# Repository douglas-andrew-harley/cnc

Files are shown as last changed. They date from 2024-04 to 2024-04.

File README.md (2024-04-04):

# FCCH CNC files

This repo contains archives of information related to the various CNC machines
at the Creator Hub. Each machine's data is in a separate top-level directory.
Within each directory, there are various sub-directories for hardware design,
software config files, etc.

## Wood-48x48

CNC Router in wood shop.

## Metal_mill

Donated 3-axis mill previously retrofitted for CNC.  The controller was old and did not work with LinuxCNC and it also was just mounted on a plate and not enclosed so we built a new controller modelled after the Wood-48x48 controller.  This folder contains the design and documentation for that new controller cabinet.

[metal_mill README](metal_mill/README.md)

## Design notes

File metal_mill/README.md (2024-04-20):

# Metal Mill CNC Controller

This project is a CNC controller for a mill or other 3 axis machaine that uses 35V-40V DC servo motors.

It consists of 2 parts

1) a controller cabinet that controls the motors in accordance to instructions from a computer running LinuxCNC and
2) an RFID and E-Stop module that connects to the controller cabinet to controll whether the servo drives are enabled.

Design File PDFs

* [metal_mill_wiring.sch (pdf)](metal_mill_wiring.pdf) (created in EagleCAD)
* [FCCH_RFID_ESTOP.sch (pdf)](FCCH_RFID_ESTOP.sch.pdf) (created in EagleCAD)
* [FCCH_RFID_ESTOP.brd (pdf)](FCCH_RFID_ESTOP.brd.pdf) (created in EagleCAD)
* [FCCH_RFID_ESTOP.brd (fab print pdf)](FCCH_RFID_ESTOP.brd.fab.pdf) (created in EagleCAD)
* [panel_cutouts.FCStd (pdf)](panel_cutouts.pdf) (created in FreeCAD)

## Controller Cabinet Components

* (1) 7i96s Controller
* (3) G320X - Gecko DC Servo Drive
* (1) NSP-1600-36 Power Supply
* (1) 12V to 5V buck Converter
* (4) Panel mount GX16-8 Aviation Connectors
* (6) Panel mount 3.5mm mono jacks with plug detection (3 terminal)
* (1) Panel mount A/C C-14 reciptical
* (3) Power Bus Bars (at least 5 position)
* (1) case (we are using a salvaged desktop PC)
* (1) panel for connectors

### 7i96s Controller

This is a card that provides IO and axis drive output for LinuxCNC.  The card connects to a PC via a point to point (no switch) dedicated Ethernet.  This project describes how the inputs and outputs of the 7i96s should be connected to interface with the mill.

Input Summary

* INPUT0: Drive Power OK<br>
  High (3.5 ~ 5.5V) : When the Vout ≦ 77% ± 5%.<br>
  Low (-0.5 ~ 0.5V) : When Vout ≧ 80% ± 5%.
* INPUT1: Drive Power T-Alarm<br>
  High (3.5 ~ 5.5V) : When the internal temperature exceeds the limit of temperature alarm, or when Fan fails.<br>
  Low (-0.5 ~ 0.5V) : When the internal temperature is normal, and when Fan normally works.
* INPUT2: Xmin limit switch (normally open)
* INPUT3: Xmax limit switch (normally open)
* INPUT4: Ymin limit switch (normally open)
* INPUT5: Ymax limit switch (normally open)
* INPUT6: Zmin limit switch (normally open)
* INPUT7: Zmax limit switch (normally open)
* INPUT8: X drive OK/Fault High==OK
* INPUT9: Y drive OK/Fault High==OK
* INPUT10: Z drive OK/Fault High==OK
* IN_COM: +5V (all inputs will be 0-5V)

Output Summary

* OUT0: Reset Drivers. Hold high for at least 1 sec to reset X,Y, and Z drivers to clear a fault on any or all drivers. INPUTs 8,9,10 read the OK/fault state of the X,Y,Z drivers respectively.
* OUT1: Motor Power Enable.
* Stepper Drive Units 0-2 connect to the 3 G320X drivers

### G320X - Gecko DC Servo Drive

The 7i96s provides stepper motor outputs for the drives but the mill we are using has DC servo motors installed.  The G320X provides translation between the stepper motor signals and DC servo motor control. Each servo motor connects to a G320X via 2 dc power wires and 4 encoder wires. The encoder provides feedback to the G320X so that it can determine what power to send to the motor to make its position match the position specified by LinuxCNC.

The G320X drives the motors with a PID controll. There are three screw pots to adjust the position, integral, and derivated gains. When the mill is operational, each axis needs to be tuned to minimize the error.

<https://www.youtube.com/watch?v=Ic4CvIOm6O4>

### NSP-1600-36 Power Supply

This PS provides up to 500W to each of the X,Y,Z drives at an adjustable voltage between 35V and 40V. The mill's X axis motor is rated at 38V and the Y axis is rated at 40V so we can adjust the voltage to 39V to split the difference. The Z axis motor is not easily accessible so we assume its either 38 or 40V. 

The main power can be turned on and off independent of the allways on aux power (12V@850ma) which we use to power all the components in the cabinet and the E-Stop RFID module.

The PS has a 16 pin connector that provides the aux power and control signals which we interface through the 7i96s so that Linux CNC can controll if the drive power is on or off and determine its status.

### 12V to 5V buck Converter

The aux power from the NSP-1600-36 is 12V but the 7i96s requires 5V.

### Panel mount GX16-8 Aviation Connectors

Each axis motor is connected to the controller cabinet via a GX16-8 Aviation connector. These connectors are panel mount and screw on for a secure connection. They are avaiable with even number of connectors. We need 7 so we got the 8 conductor. 

We terminate two separate cables into the GX16-8

1) 14 gauge 2 conductor cable for motor power A 38V@500W motor can draw up to 12.5A which requires 14 gauge wires for the 2 motor power wires. 
2) 22 gauge 5 conductor cable for the motor encoder signals and a separate motor housing ground wire. The encoder on these motors use single ended singles so require 4 wires. Since the encoders are single ended (not differential), the encoder cables should be shielded with the shield connected to the case ground on the cabinet side and left unconnected on the motor side. The encoder cable should also have a 5th conductor which is connected to the power supply ground in the cobinet and to the motor housing.

### Panel mount 3.5mm mono jacks with plug in detection

The limit switches are connected to the controller cabinet via 3.5mm mono plugs/jacks. 3 terminal jacks are used where the third terminal makes contact with the tip terminal when no jack is inserted. This is used so that when the jack is removed, it will complete the circuit as if the limit switch was activated. This makes it so that if a limit switch is removed, LinuxCNC will think that the limit switch is tripped and will not drive the machine in that direction. 

### Panel mount A/C C-14 reciptical

This is a stanard reciptical for connecting a device to building power.

### Power Bus Bars

To be sourced...

To connect components to GND, +5V and +12V, we use 3 bus bars that can terminate bare wire leads.

### Case

We are using an old desktop PC from a thrift store.  An alarm panel case or similar would also be suitable.

### Panel for connectors

The file [panel_cutouts.FCStd](panel_cutouts.pdf) (created with FreeCAD) documents the panel cutouts to accept the various panel mount jacks the cabinet uses to connect to the motors, limit switches, FCCH_RFID_ESTOP_module, power, and Ethernet to the computer running LinuxCNC

## Controller Cabinet Cable Harnesses

Inside the controller cabinet, all components are connected via the following wire harnesses. The Wn label of each harness refers to the designation in the schematic.

The schematic [metal_mill_wiring.sch (pdf)](metal_mill_wiring.pdf) (created in EagleCAD) documents the connections.

### Cables required

* 22 gauge 6 conductor cable
* 22 gauge 4 conductor cable
* 22 gauge 2 conductor cable
* 22 gauge single black wire
* 18 gauge 2 conductor red/black
* 18 gauge 3 conductor red/orange/black
* 14 gauge 2 conductor red/black
* 14 gauge 3 conductor line cord

### (W1) Stepper and reset cables from 7i96s to each of the G320X servo drives

3 needed
bare leads to bare leads

* 22 gauge 4 conductor cable
  * one end: bare leads into the terminals on the G320X's
    * cable shield: no connection (only connect on other end)
    * black:  COM
    * blue:   STEP
    * yellow: DIR
    * orange: ERR/RES
  * other end: bare leads into the 7i96s TB3 and TB3 terminals (see schematic)
    * cable shield: connect to chassis ground screw located near the 7i96s
    * black:  TB1 GND(n)
    * blue:   TB1 STEP(n)+
    * yellow: TB1 DIR(n)+
    * orange: TB3 INPUT8 (ERR/RES input)

Build Notes:

We used a shielded 8 conductor wire because the maker space had a big spool of it. The 4 unused conductors were cut short and sealed under a short piece of heat shrink.

On the 7i96s end, the orange and shield wires need to be about 4 inches longer than the others because they go to different places. Strip 5 inches of the cable insulation. cut black,blue,yellow wires to about 1.25 inches. Heat shrink a 3/8 inch tube so that half is over the insulation and half is over the protrubing wires. 

On the G320X end, the orange wire needs to be longer than the others by about an inch. Strip a little over 2 inches of insulation. Cut the shield wire short to the insulation (wont be connected on this end). Cut the black,blue, and yellow wires to about an inch. Heat shrink about 3/8 inch tube over the insulation and wires.

### (W2) Motor Power and Encoder Jacks

3 needed
GX16-8 Aviation connector to 3 separate cables with bare leads

* 14 gauge 2 conductor red/black
  * one end: solder to GX16-8
    * black: terminal 1
    * red:   terminal 2
  * other end: bare leads screw into G320X terminals
    * black: arm-
    * red:   arm+
* 22 gauge 4 conductor cable
  * one end: solder to GX16-8
    * C1: terminal 4
    * C2: terminal 5
    * C3: terminal 6
    * C4: terminal 7
  * other end: bare leads to G320X screw terminals
    * C1: ENC_GND
    * C2: ENC_5VDC
    * C3: Channel_A
    * C4: Channel_B
* 22 gauge single black wire
  * one end: solder to GX16-8
    * terminal 8
  * other end connects to the 9 position gnd bus bar located near the panel

### (W3) E-Stop and RFID Module Jacks

1 needed
GX16-8 Aviation connector to 2 separate cables

* 18 gauge 3 conductor red/orange/black
  * one end: solder to GX16-8
    * black:  terminal 1
    * red:    terminal 2
    * orange: terminal 3
  * other end: bare leads to GND,+5V, and +12V bus bars
* 22 gauge 6 conductor cable
  * one end: solder to GX16-8
    * C1: terminal 4
    * C2: terminal 5
    * C3: terminal 6
    * C4: terminal 7
    * C5: terminal 8
    * C6: N/C

### (W4) Limit Switch Panel Mount Jacks

1 needed
6x 3.5 mono panel mount jacks to 6x ground wires and 1x 6 conductor cables with bare leads

* 6x 22 gauge single black wire connects each jack terminal 1 and 2 and then to the 9 position gnd bus bar located near the panel.
* 1x 22 gauge 6 conductor cable
  * one end: solder to terminal 3 on each jack
  * other end: bare leads connect to 7i96s screw terminals
    * Xmin: TB3.3 (INPUT2)
    * Xmax: TB3.4 (INPUT3)
    * Ymin: TB3.5 (INPUT4)
    * Ymax: TB3.6 (INPUT5)
    * Zmin: TB3.7 (INPUT6)
    * Zmax: TB3.8 (INPUT7)

### (W5) Servo Driver Power

1 needed
2 circular lug crimp connectors to 3x 2 conductor cables with bare leads

* 3x 14 gauge 2 conductor red/black
  * one end collect the 3 red wires together into a circular crimp lug connector. do the same with the balck cables. The two circular connects will be bolted to the main PS lugs
  * other ends of the 3 cables has bare leads to screw into the PWR_GND (black) and 18V_to 80V_PWR terminal of the 3 G320X servo drivers

### (W6) A/C Input to PS

1 needed
crimp spade connectors to crimp spade connectors

* 14 gauge 3 conductor line cord

### (W7) Power Supply signals

1 needed
HRS DF11-16DS 16 pin IDC to bare leads

* 18 gauge 2 conductor red/black
  * one end: IDC pins inserted in 16x connector
    * red  : pin 1
    * black: pin 2
  * other end: bare leads to GND and 12V bus bars
* 22 gauge 4 conductor cable
  * one end: IDC pins inserted in 16x connector
    * C1: pin 3
    * C2: pin 4
    * C3: pin 5
    * C4: pin 6
  * other end: bare leads screwed into 7i96s terminals
    * C1: TB3-16 (OUT1+)
    * C2: TB3-15 (OUT1-)
    * C3: TB3-1  (INPUT0)
    * C4: TB3-2  (INPUT1)

Note that the DF11-16DS connector on the PS has 16 positions. 1-6 are connected as above. In addition, two loop back wires on the connector are needed to connect positions 13 to 15, and 14 to 16. The PS came with a connector that had these loop back wires already installed. These loopback wires implement the local voltage sensing as described in the datasheet. If we ever want to implement remote sensing to compensate for drops seen at the motors, we would replace theses loopbacks with wires connecting 15 and 16 to the + and - motor leads.

### (W8) 7i96s Power

1 needed
bare leads to bare leads

* 18 gauge 2 conductor red/black

## E-Stop and RFID Module (FCCH_RFID_ESTOP)

This is a custom PCB in a separate enclosure that can be mounted in a accessible location on the mill for the operator to interact with. The enclosure contains this custom PCB and also the FCCH RFID PCB. An 8 pin GX16-8 Aviation connector connects this enclosure with the controller cabinet.

The FCCH_RFID_ESTOP module provides two functions.

1) RFID Authorization. Major machines at the FCCH (fort Collins Creator Hub) have RFID based access control. When an authorized RFID tag is not present in the V slot of this module, the axis motors are inhibited.
2) E-Stop switch. If the E-Stop is pressed, the axis motors are inhibited.

The ERR/RES lines of the G320X drivers are brought to this module. They are attached to ground (which inhibits the drivers) through the normally closed contacts of a safety relay. When both a valid RFID tag is present and the E-Stop switch is not active, the relay is energized, breaking the connection to ground and enabling the drivers.

The file [FCCH_RFID_ESTOP.sch (pdf)](FCCH_RFID_ESTOP.sch.pdf) contains the schematic for the custom PCB and [FCCH_RFID_ESTOP.brd (pdf)](FCCH_RFID_ESTOP.brd.pdf) is the board layout.

For physical dimensions of the board refer to [FCCH_RFID_ESTOP.brd.fab.pdf](FCCH_RFID_ESTOP.brd.fab.pdf)

## FCCH_RFID_ESTOP Cable Harnesses

### (EW1) GX16-8 connector to FCCH_RFID_ESTOP board

1 needed
GX16-8 panel mount side to bare leads

* Ethernet cable soldered to the panel mount. Wires connected per schematic to screw terminals of the FCCH_RFID_ESTOP board.

### (EW2) FCCH_RFID_ESTOP board to FCCH_RFID board

1 needed
bare leads to bare leads

* 22 gauge 4 conductor cable

### (EW3) Controller Cabinet to FCCH_RFID_ESTOP module

1 needed
GX16-8 to GX16-8

Ethernet cable soldered to the free hanging side of the GX16-8 connects. All pins pass through straight.

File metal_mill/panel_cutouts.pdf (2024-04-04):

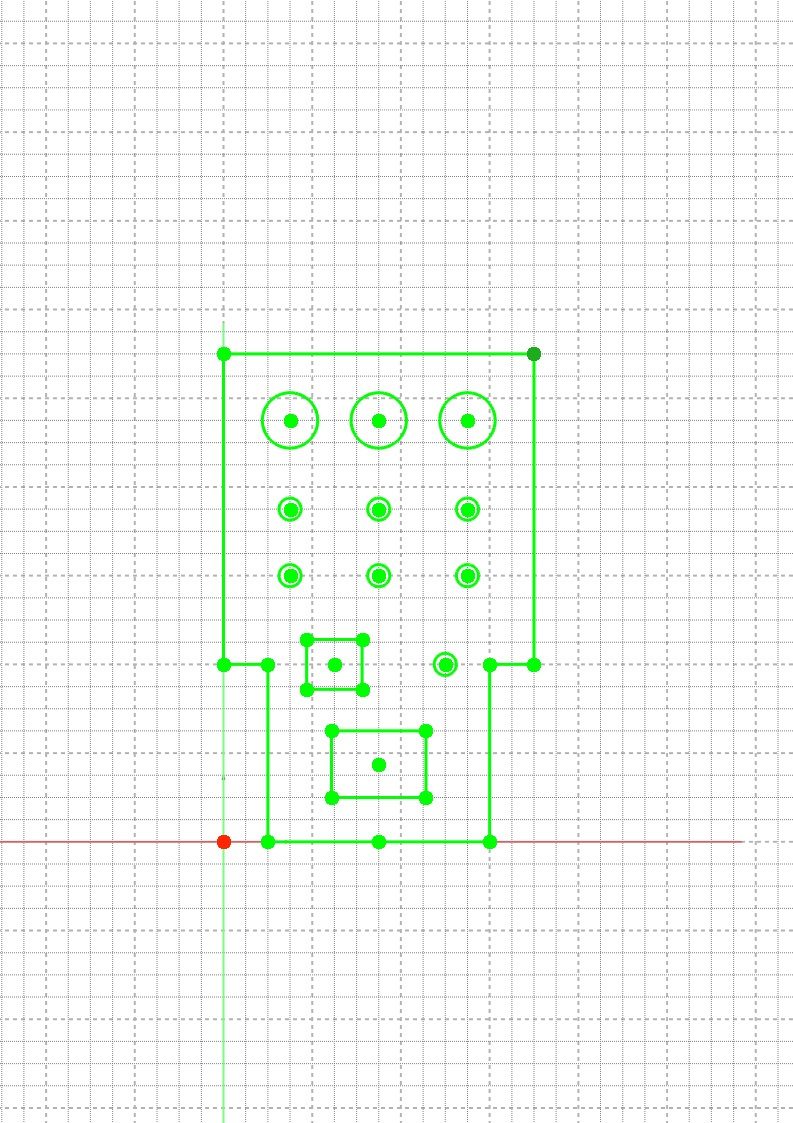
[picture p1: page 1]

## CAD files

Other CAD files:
metal_mill/panel_cutouts.FCStd

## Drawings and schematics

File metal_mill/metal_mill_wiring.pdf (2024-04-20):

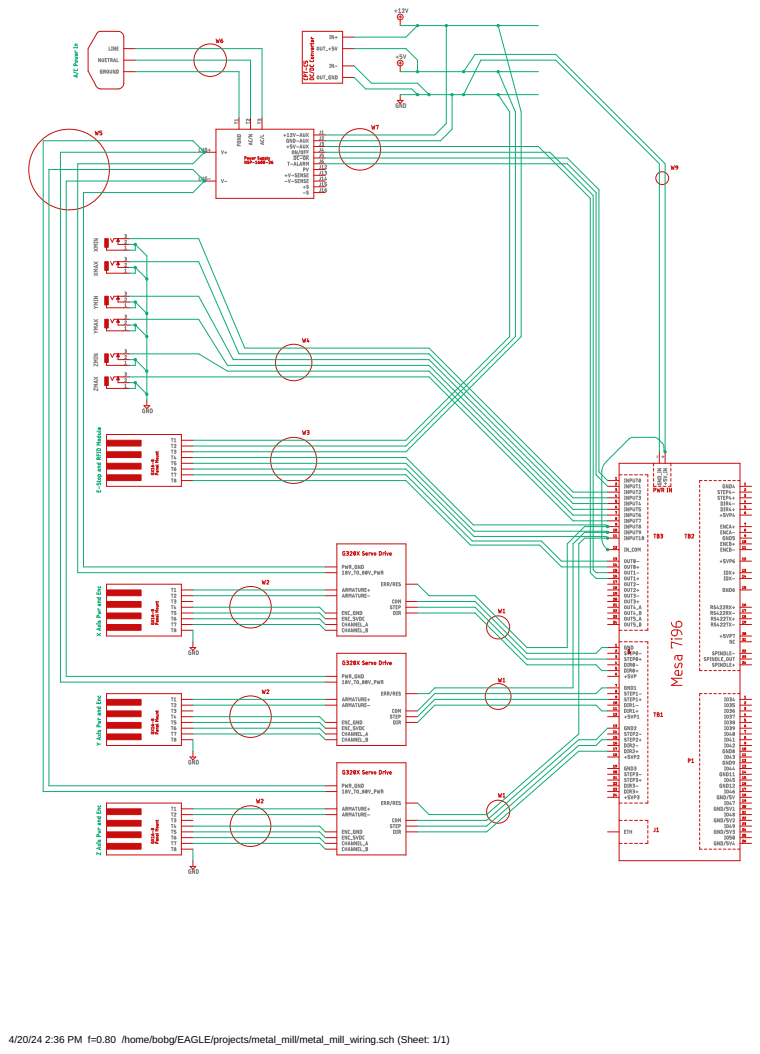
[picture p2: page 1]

4/20/24 2:36 PM f=0.80 /home/bobg/EAGLE/projects/metal_mill/metal_mill_wiring.sch (Sheet: 1/1)

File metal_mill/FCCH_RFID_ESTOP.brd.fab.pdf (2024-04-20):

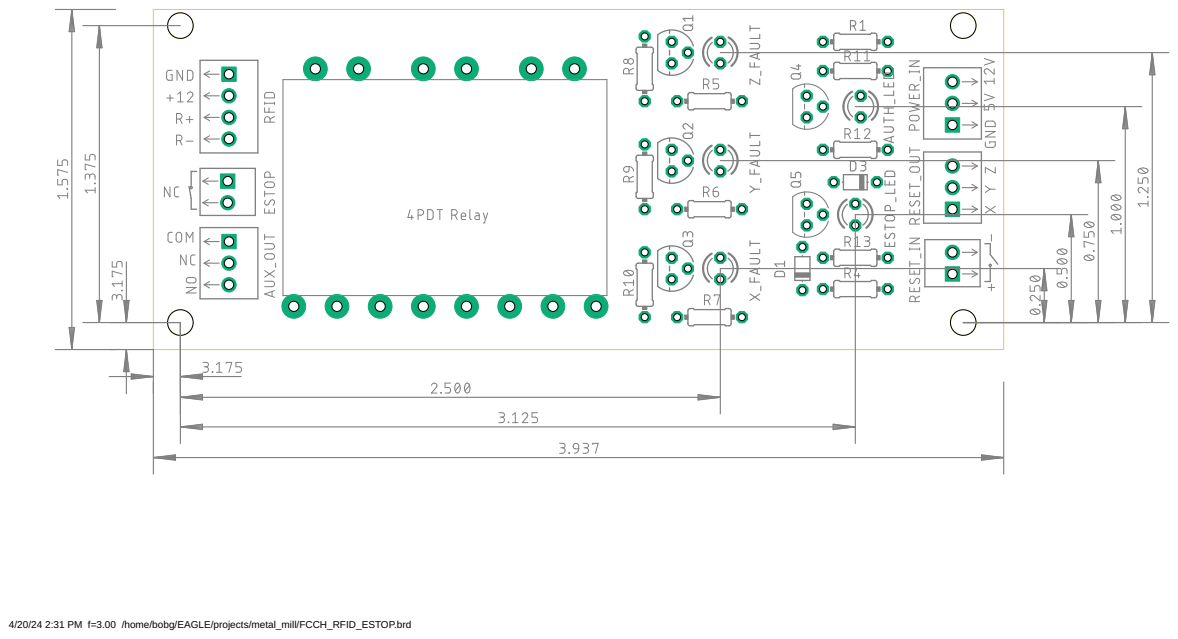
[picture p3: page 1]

4/20/24 2:31 PM f=3.00 /home/bobg/EAGLE/projects/metal_mill/FCCH_RFID_ESTOP.brd

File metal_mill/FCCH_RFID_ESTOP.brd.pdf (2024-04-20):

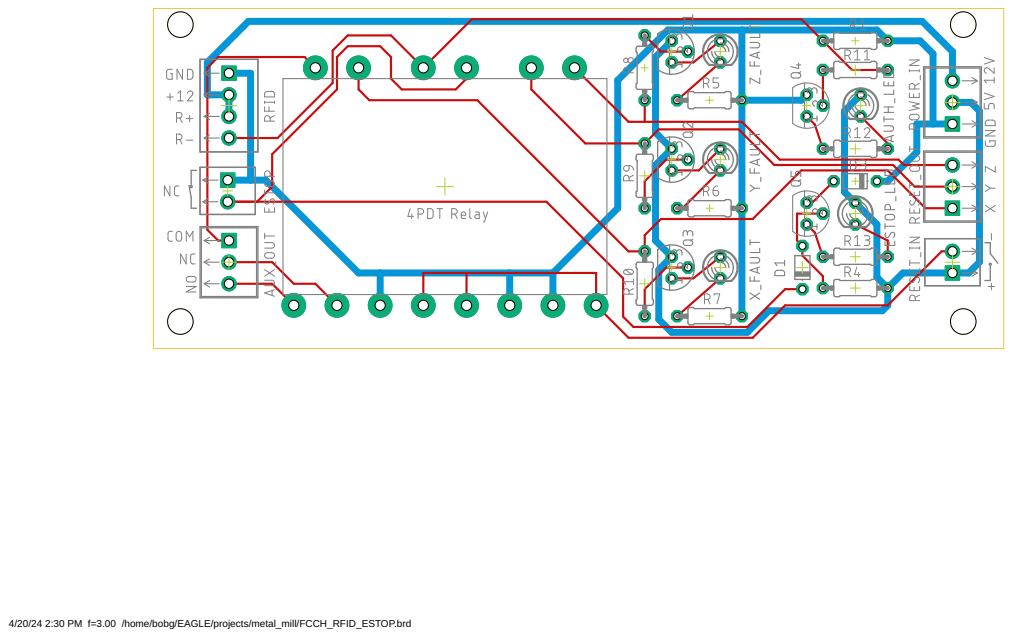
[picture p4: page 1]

4/20/24 2:30 PM f=3.00 /home/bobg/EAGLE/projects/metal_mill/FCCH_RFID_ESTOP.brd

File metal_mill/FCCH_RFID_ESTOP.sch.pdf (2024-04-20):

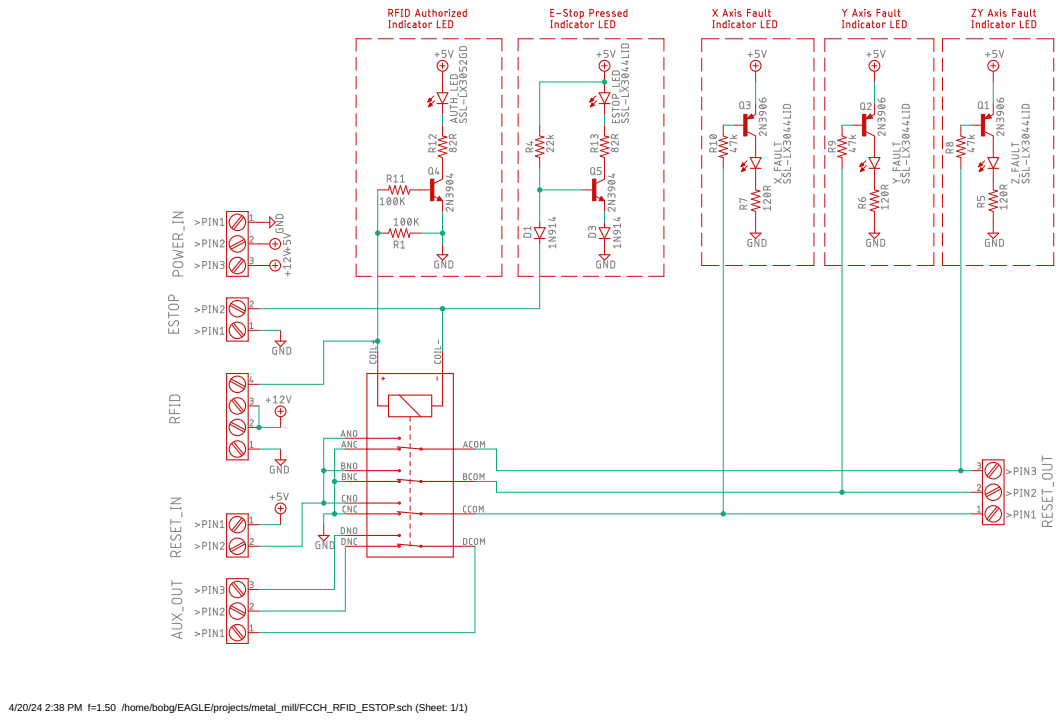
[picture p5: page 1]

4/20/24 2:38 PM f=1.50 /home/bobg/EAGLE/projects/metal_mill/FCCH_RFID_ESTOP.sch (Sheet: 1/1)

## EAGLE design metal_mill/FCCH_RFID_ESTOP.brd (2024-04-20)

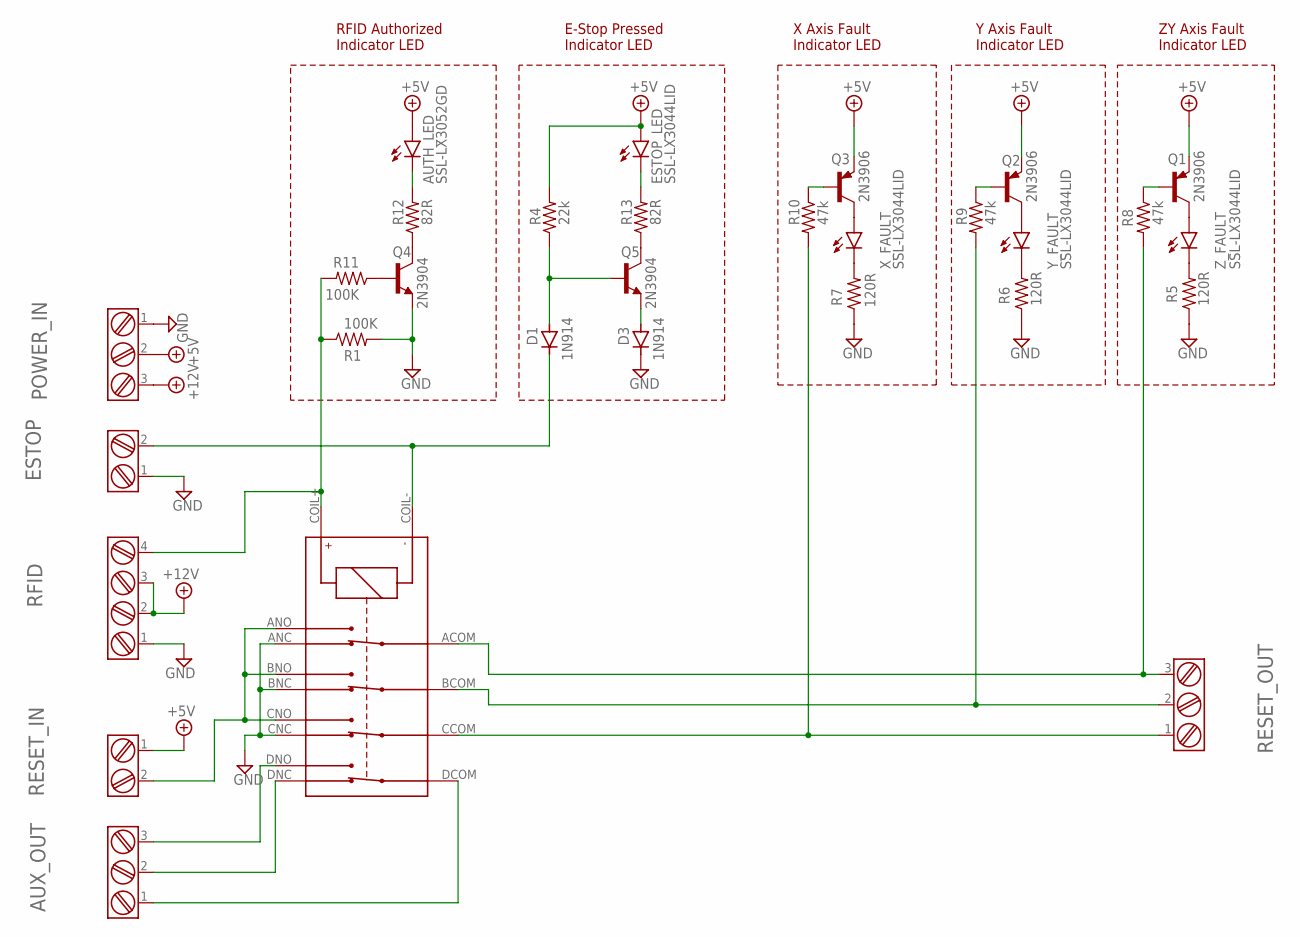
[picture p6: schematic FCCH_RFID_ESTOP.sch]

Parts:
AUTH_LED: SSL-LX3052GD; LED3MM
AUX_OUT: EURO-CON-3_2.54P; CONN3-2.54P
D1, D3: 1N914; D-5
ESTOP: EURO-CON-2_2.54P; CONN2_2.54P
ESTOP_LED: SSL-LX3044LID; LED3MM
POWER_IN: EURO-CON-3_2.54P; CONN3-2.54P
Q1, Q2, Q3: 2N3906; TO92
Q4, Q5: 2N3904; TO92
R1, R11: 100K; 0204/7
R4: 22k; 0204/7
R5, R6, R7: 120R; 0204/7
R8, R9, R10: 47k; 0204/7
R12, R13: 82R; 0204/7
RESET_IN: EURO-CON-2_2.54P; CONN2_2.54P
RESET_OUT: EURO-CON-3_2.54P; CONN3-2.54P
RFID: EURO-CON-4_2.54P; CONN4-2.54P
U$1: NC4D-JP-DC5V; NC4D-JP
X_FAULT: SSL-LX3044LID; LED3MM
Y_FAULT: SSL-LX3044LID; LED3MM
Z_FAULT: SSL-LX3044LID; LED3MM

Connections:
+5V: AUTH_LED.A, ESTOP_LED.A, POWER_IN.2, Q1.3 (E), Q2.3 (E), Q3.3 (E), R4.2, RESET_IN.1
+12V: POWER_IN.3, RFID.2, RFID.3
AUX_RELAY_COM: AUX_OUT.1, U$1.DCOM
AUX_RELAY_NC: AUX_OUT.2, U$1.DNC
AUX_RELAY_NO: AUX_OUT.3, U$1.DNO
ESTOP: D1.C, ESTOP.2, U$1.COIL-
GND: D3.C, ESTOP.1, POWER_IN.1, Q4.3 (E), R1.2, R5.1, R6.1, R7.1, RFID.1, U$1.ANC, U$1.BNC, U$1.CNC
unnamed: R7.2, X_FAULT.K (C)
unnamed: RESET_IN.2, U$1.ANO, U$1.BNO, U$1.CNO
unnamed: Q4.1 (C), R12.1
unnamed: Q4.2 (B), R11.1
unnamed: D1.A, Q5.2 (B), R4.1
unnamed: Q5.1 (C), R13.1
unnamed: D3.A, Q5.3 (E)
unnamed: Q3.1 (C), X_FAULT.A
unnamed: R6.2, Y_FAULT.K (C)
unnamed: Q2.1 (C), Y_FAULT.A
unnamed: R5.2, Z_FAULT.K (C)
unnamed: Q1.1 (C), Z_FAULT.A
unnamed: ESTOP_LED.K (C), R13.2
unnamed: Q3.2 (B), R10.1
unnamed: AUTH_LED.K (C), R12.2
unnamed: Q2.2 (B), R9.1
unnamed: Q1.2 (B), R8.1
RFID_ENABLE: R1.1, R11.2, RFID.4, U$1.COIL+
X_ERR/RES: R10.2, RESET_OUT.1, U$1.CCOM
Y_ERR/RES: R9.2, RESET_OUT.2, U$1.BCOM
Z_ERR/RES: R8.2, RESET_OUT.3, U$1.ACOM

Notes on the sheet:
E-Stop Pressed Indicator LED
RFID Authorized Indicator LED
X Axis Fault Indicator LED
Y Axis Fault Indicator LED
ZY Axis Fault Indicator LED

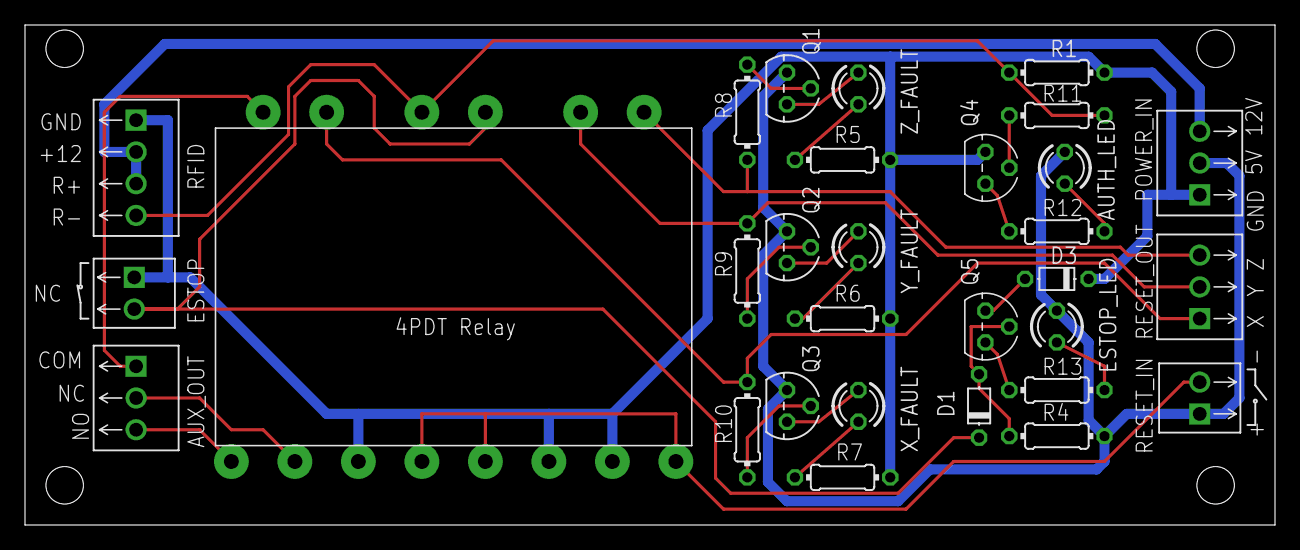
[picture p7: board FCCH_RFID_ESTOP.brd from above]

Board: 2 copper layers, 100.0 x 40.0 mm, 30 parts (0 on the bottom side), 28 nets.

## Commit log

2024-03-31 initial commit of metal_mill project folder
    [fcch-7i96-dm556-controller copy.dxf, fcch-mill-ctrl-wiring.dxf, metal_mill_wiring.sch]
2024-04-04 First fully documented commit. Some details like the FCCH_RFID_ESTOP board layout still need to be done.
    [FCCH_RFID_ESTOP.sch, metal_mill_wiring.sch]
2024-04-04 added pdf's so that people can review the schematics without having EagleCAD
    [fcch-7i96-dm556-controller copy.dxf, fcch-mill-ctrl-wiring.dxf, panel_cutouts.FCStd]
2024-04-04 metal_mill: changed schematic and CAD file links in the README.md to open the corresponding pdf files to make it easier to browse the project
2024-04-07 Added FCCH_RFID_ESTOP board layout and wire harnesses description in README.md
    [FCCH_RFID_ESTOP.brd, FCCH_RFID_ESTOP.sch]
2024-04-15 check point: before changing the reset relay to allow +5V as well as ground
    [FCCH_RFID_ESTOP.brd, FCCH_RFID_ESTOP.sch]
2024-04-15 * changed reset_in to use the NO contacts of the relay * grouped the screw terminals that will connect to the GX16-8
    [FCCH_RFID_ESTOP.brd, FCCH_RFID_ESTOP.sch]
2024-04-20 fixed some mistakes found by prototyping on a breadboard. * moved wire terminals to the end of the board * updated LED devices (was using a header) * updated resistor values
    [FCCH_RFID_ESTOP.brd, FCCH_RFID_ESTOP.sch, metal_mill_wiring.sch]
